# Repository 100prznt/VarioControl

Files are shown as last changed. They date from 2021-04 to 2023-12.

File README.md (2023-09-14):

Temp2IoT wiring

# VarioControl
IoT pump control for Vario pumps with 0 - 10 V interface.

------------

## Current build state

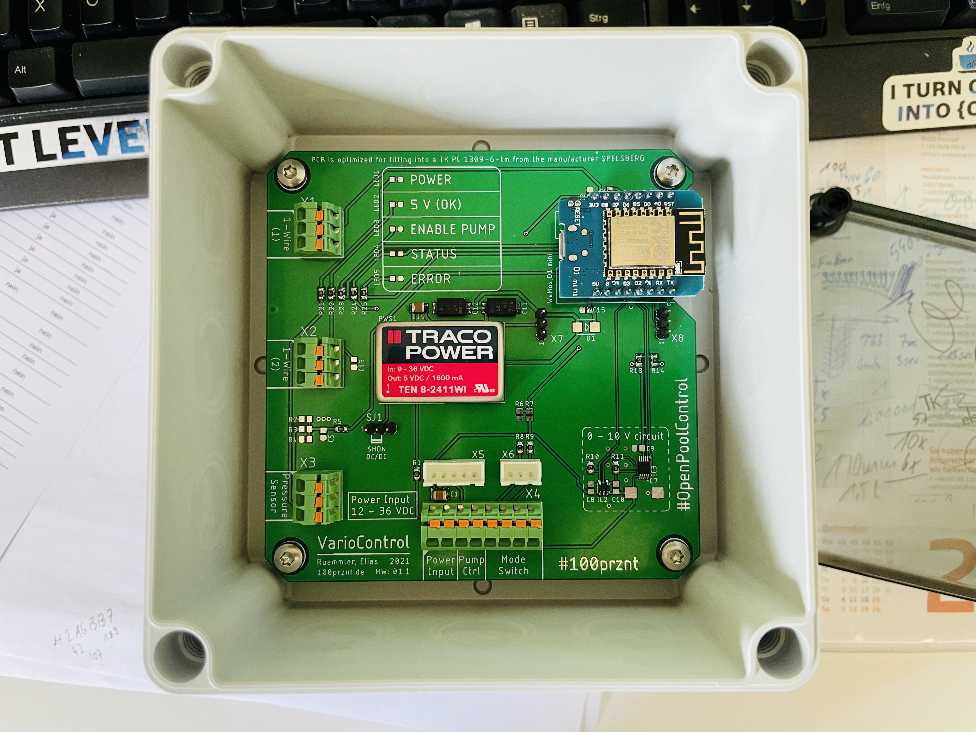
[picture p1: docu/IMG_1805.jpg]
VarioControl PCB v1.1 in Spelsberg enclosure

Unassembled PCB in matching Spelsberg enclosure. (2021/06/06)

## Hardware Features

+ 0 - 10 V interface for speed control of a Vario pump
+ WiFi interface
+ 1-wire interface for two DS18B20 temperature sensors
+ 0 - 10 V input for a pressure sensor (alt. also 0 - 5 V or 4 - 20 mA possible)
+ Switch input for operating mode preselection (AUTO - OFF - MANUAL)
+ 5 LEDs for status visualization
+ Wide range power supply (12 - 36 V)

## PCB

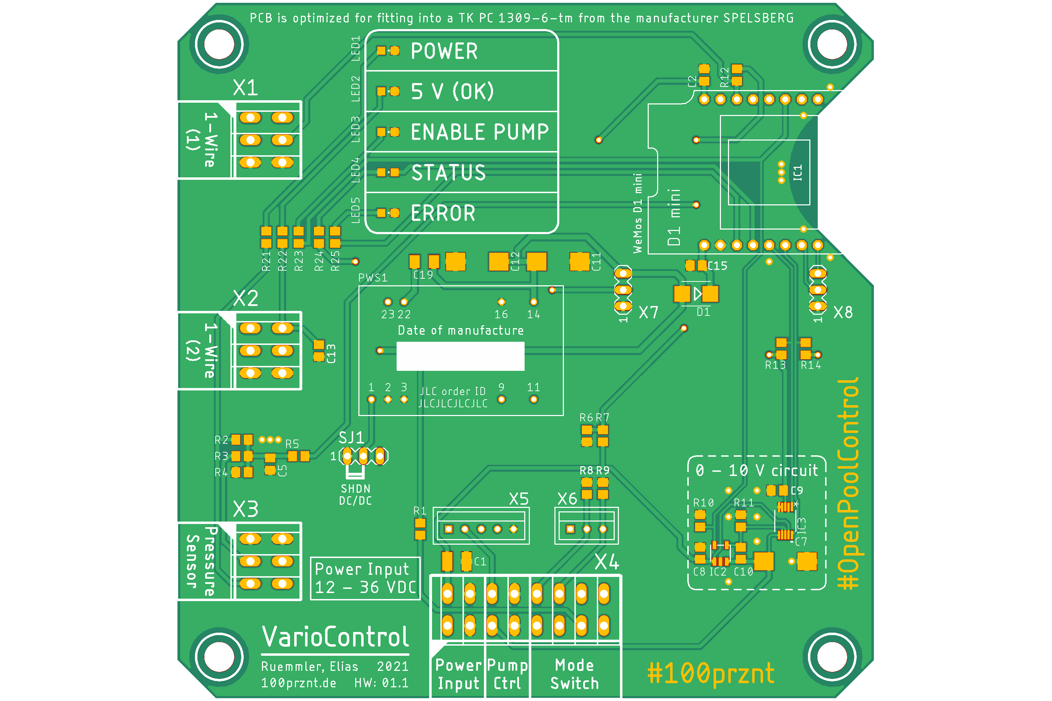
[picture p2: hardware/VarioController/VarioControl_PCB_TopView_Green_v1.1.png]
VarioControl PCB TopView v1.1


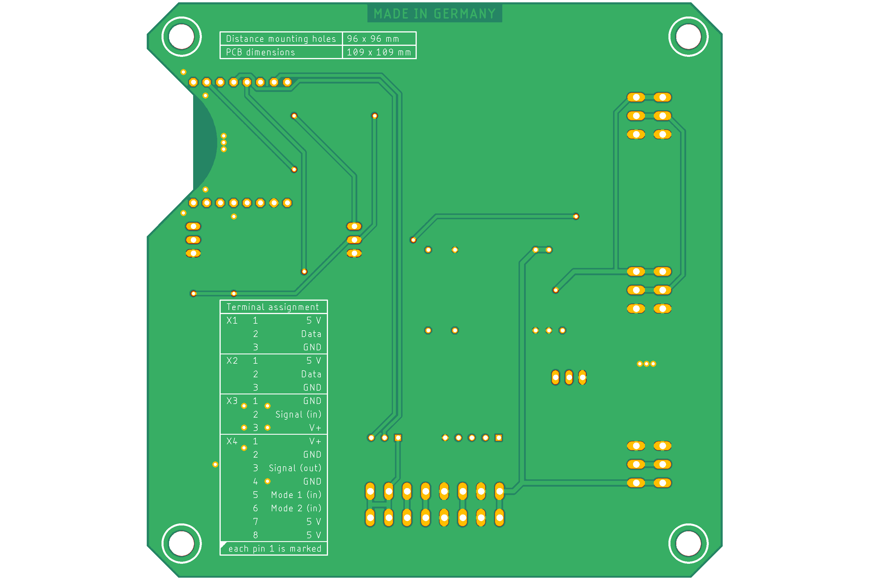
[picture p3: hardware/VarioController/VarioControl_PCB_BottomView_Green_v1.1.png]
VarioControl PCB BottomView v1.1


## AquaTechnix AquaVarioPlus

### Setup

The external control of the AquaVarioPlus can be activated in the setup menu of the pump. This is described in detail in the manual (of the BADU Eco Soft, which has the same control) on page 9 an 10. The "Steuerart" (control type) 0 - 10 V, code 3 is required.

* [Manual BADU EcoSoft](docu/BA_BADU_EcoSoft.pdf)

### Connector

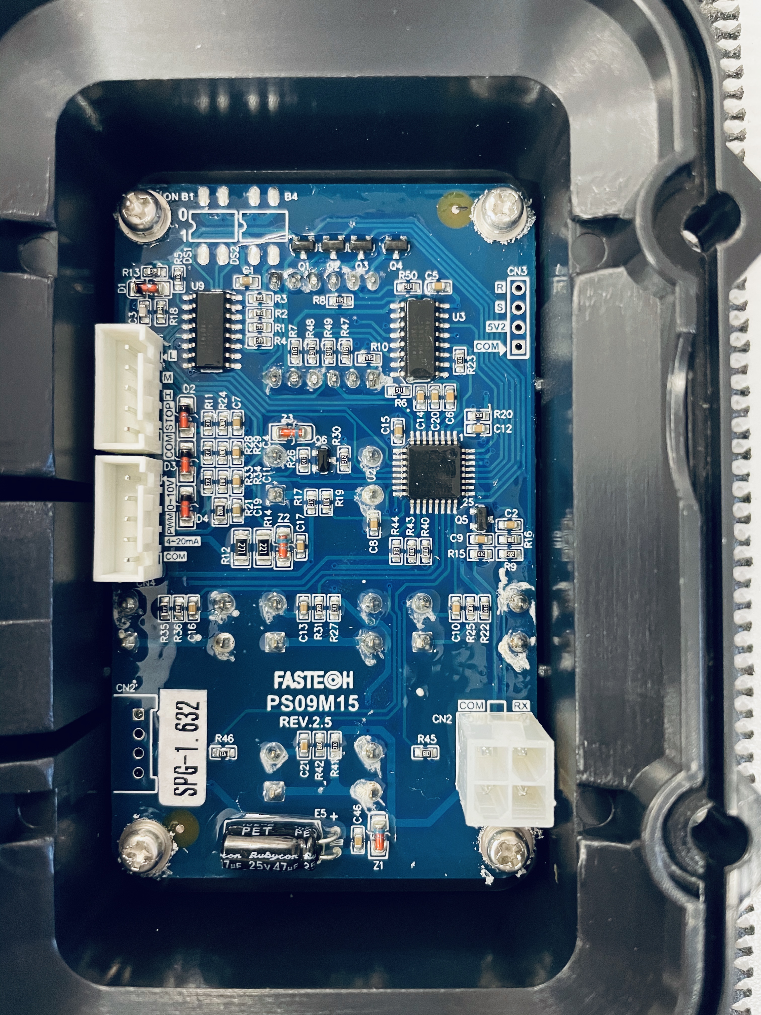
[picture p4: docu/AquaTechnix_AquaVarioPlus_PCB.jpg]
AquaVarioPlus PCB

Control board of the AquaVarioPlus pump from AquaTechnix.

The CN4 (pin 2) connector is provided for controlling the pump via the 0 - 10 V interface. See also [Manual BADU EcoSoft](docu/BA_BADU_EcoSoft.pdf) on page 7.

#### Pinning

| pin# | function | specification | in use with VarioControl | 
|-----:|:---|:---|:---:|
| 1 | n/a | | :heavy_multiplication_x: |
| 2 | rpm value (U) | 0 - 10 V | :heavy_check_mark: |
| 3 | PWM | unknow specs? | :heavy_multiplication_x: |
| 4 | rpm value (I) | 4 - 20 mA | :heavy_multiplication_x: |
| 5 | GND | | :heavy_check_mark: |

The control via the "PWM" input I have experimented with a frequency generator with various settings, unfortunately without success. I believe that the software implementation and a corresponding preselection of the control type is missing here.

#### Type
The plug used is probably a clone of the JST XH connector series, which has been modified to add an external locking mechanism. Plugs of this type are tricky to find, but an original XH plug from JST fits and holds very well.

| Manufacturer | SKU |
|:---|:---|
| JST (JAPAN SOLDERLESS TERMINALS) | __XHP-5__ |

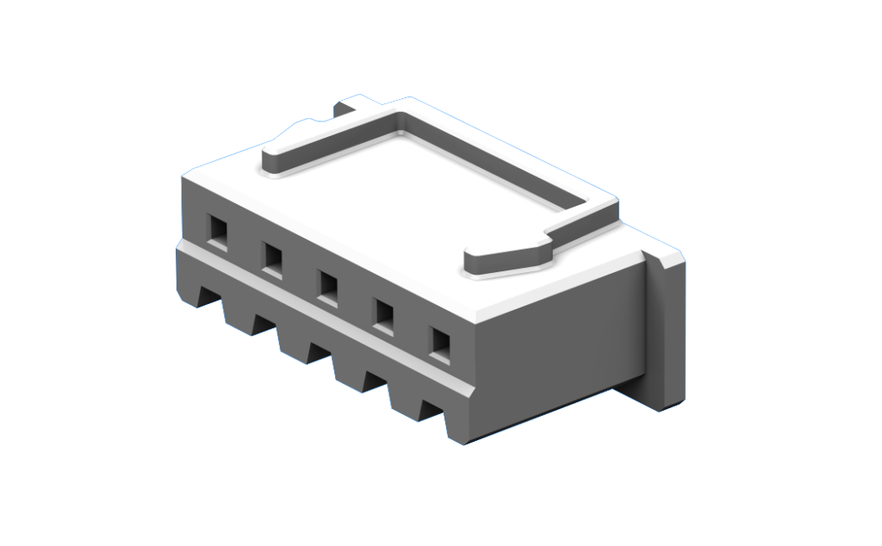
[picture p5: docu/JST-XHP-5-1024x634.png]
JST XHP-5.png


Suitable contacts are listed in the data sheet on page 2.

* [Datasheet JST XH Connector](docu/jst-xh.pdf)

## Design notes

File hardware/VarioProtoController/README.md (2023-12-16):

# ESPHome VarioProtoController

Um die Integration des __Vario Controllers__ in Home Assistant zu vereinfachen, soll die Hardware vollumfänglich mit __ESPHome__ kompatibel sein.

## Referenzen
* [Home Assistant](https://www.home-assistant.io/)
* [ESPHome](https://esphome.io/)

## BOM
Alle Komponenten des Prototyps kommen vom Hersteller DFRobot und können ohne Löten* miteinender verbunden werden.
* DAC 0-10 V [DFR0971](https://www.dfrobot.com/product-2613.html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)
* ADC [DFR0553](https://www.dfrobot.com/product-1730.html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)
* IO Shild [DFR0762](https://www.dfrobot.com/product-2395.html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)
* ESP32 [DFR0654](https://www.dfrobot.com/product-2231.html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)
* DS18B20 [KIT0021](https://www.dfrobot.com/product-1354.html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)

\*) Für den Anschluss der Temperatursensoren (DS18B20) ohne das DFRobot Gravity Shild müssen die Sensoren direkt mit einem entsprechenden Stecker (3-pin 2,54 mm) versehen werden.

## Aufbau
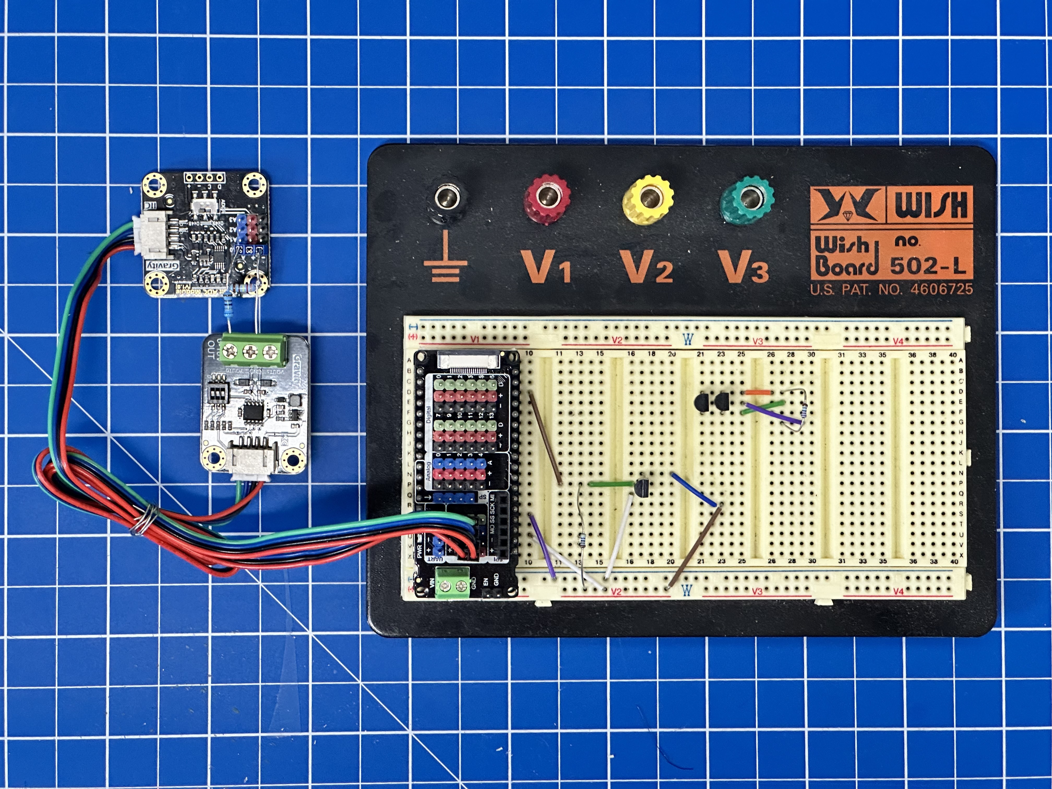
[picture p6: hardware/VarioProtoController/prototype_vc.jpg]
Aufbau der Komponenten


## Funktionen
### Übersicht
* Steuerung der Pumpe über 0 - 10 V Schnittstelle
* Eingang für 4 analoge Sensoren (z.B. Drucksensoren)
* Temperaturerfassung mit DS18B20 Sensoren

### DAC

### ADC
* Eingangsspannung ADS1115 min.: GND – 0.3
* Eingangsspannung ADS1115 max.: VDD + 0.3

Für den Anschluss von Sensoren mit 0 - 10 V Schnittstelle ist ein Spannungsteiler vorzusehen.

## ESPHome
https://community.home-assistant.io/t/esphome-configuration-for-pwm-to-0-10v-output-sensor-and-control/296445/8

### Sensoren
* Drehzahl
* Druck (1)
* Temperatur (1)

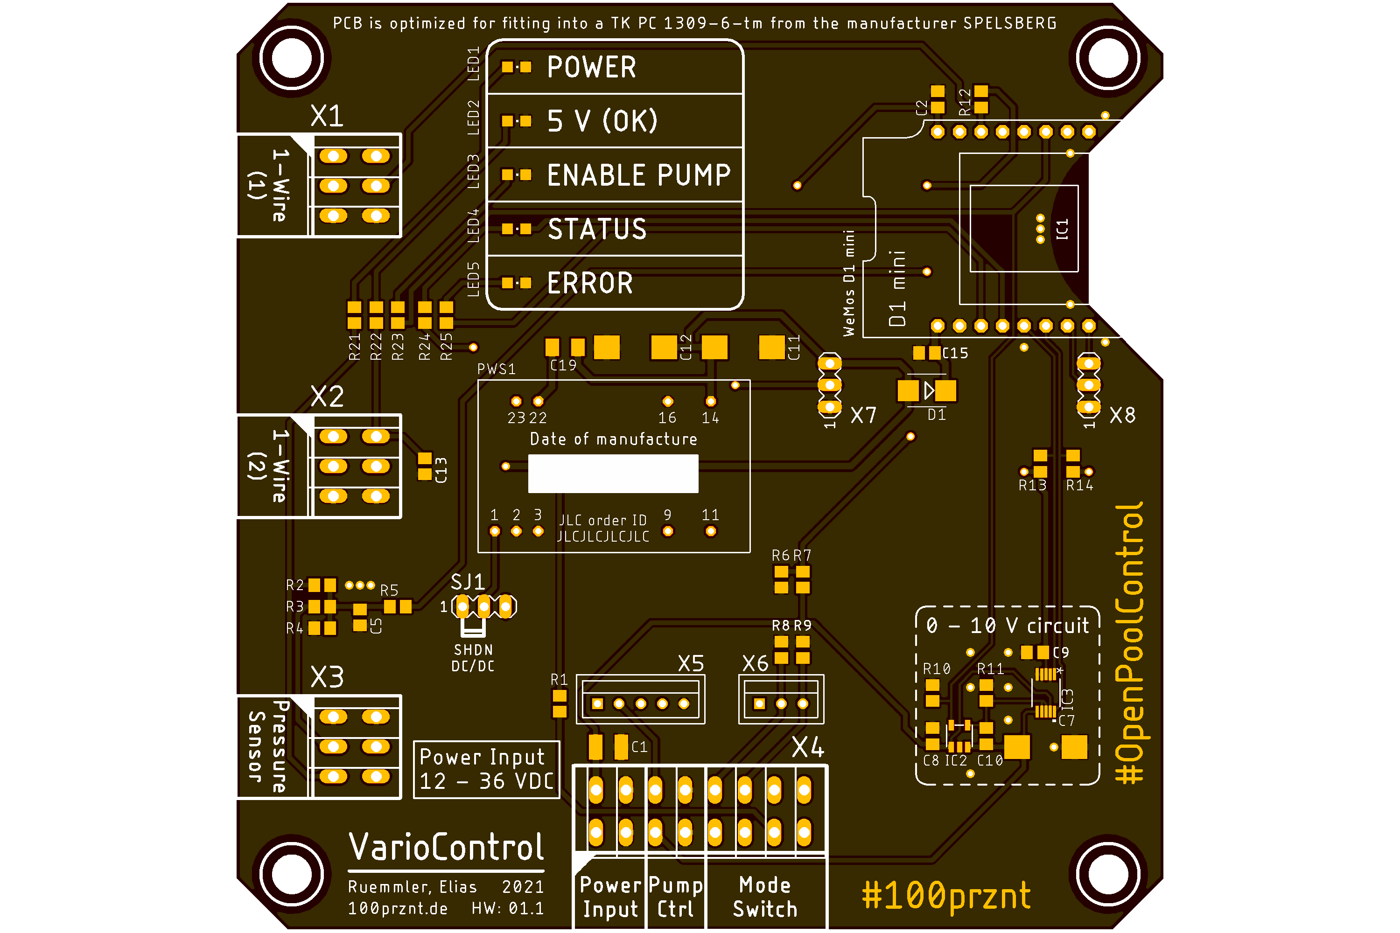
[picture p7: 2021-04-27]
hardware/VarioController/VarioControl_PCB_TopView_Black_v1.1.png

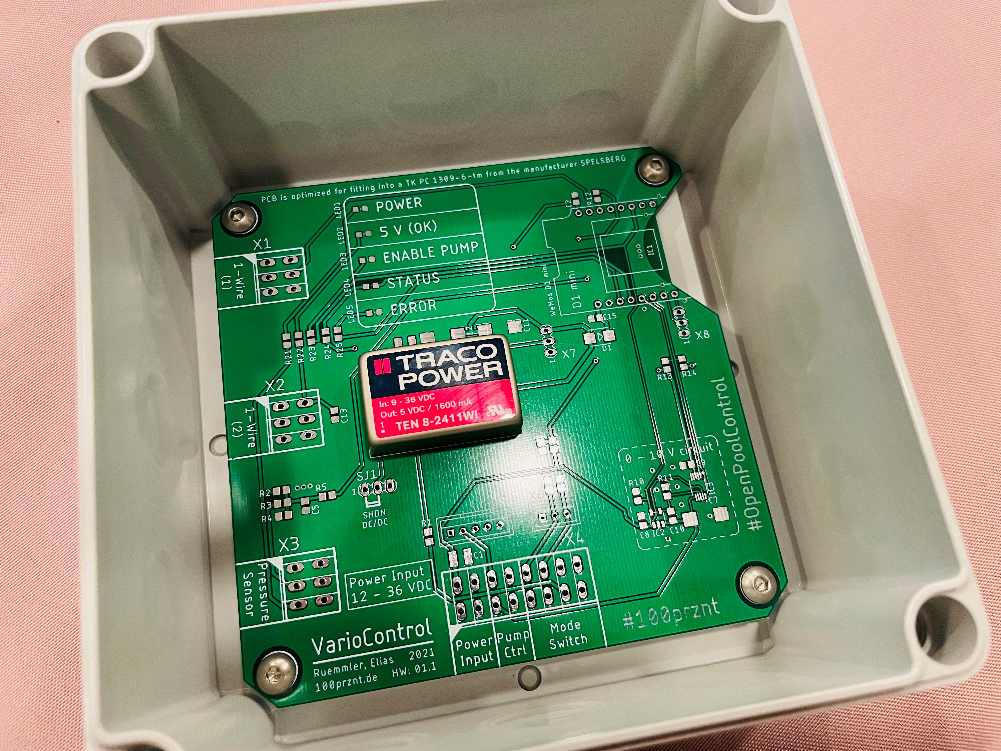
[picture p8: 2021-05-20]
docu/PCB_Unbestueckt_HW01_1_landscape.jpg

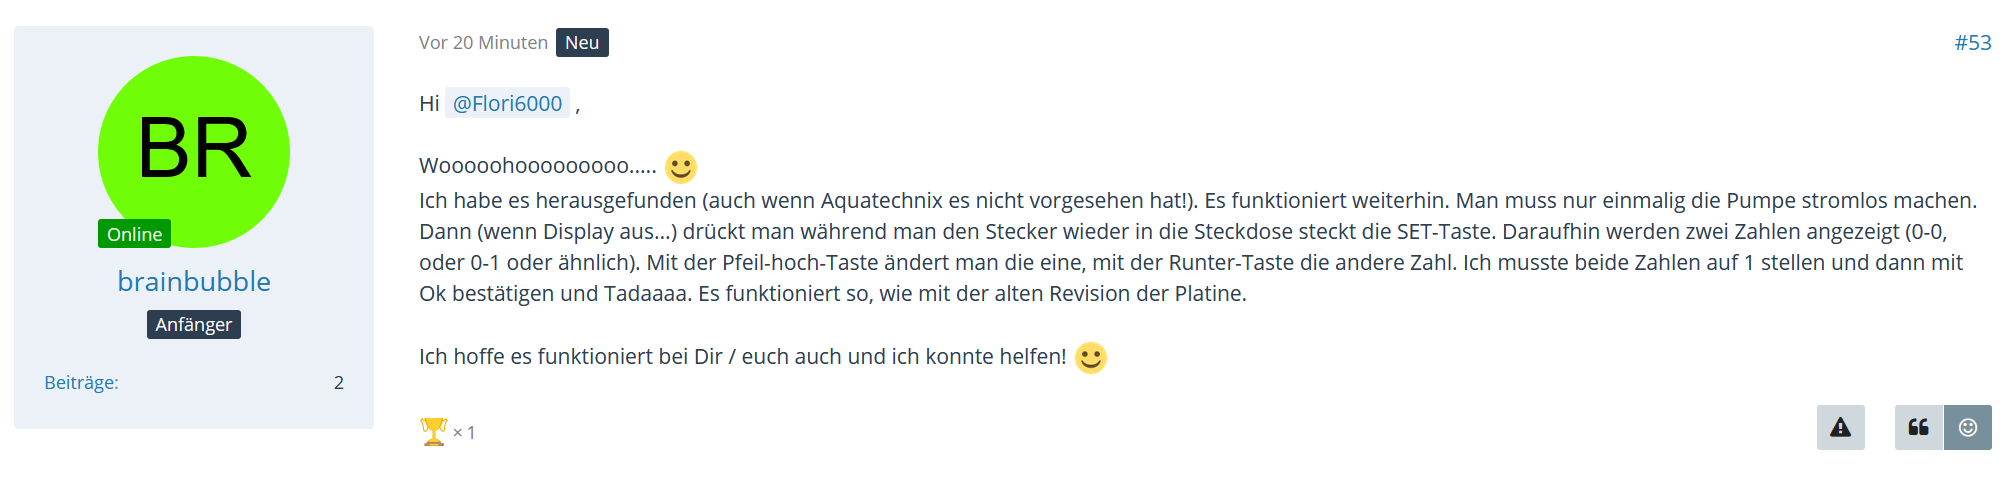
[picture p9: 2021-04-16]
docu/PPS_F_Hinweis_Umstellung_AquaVarioPlus.png

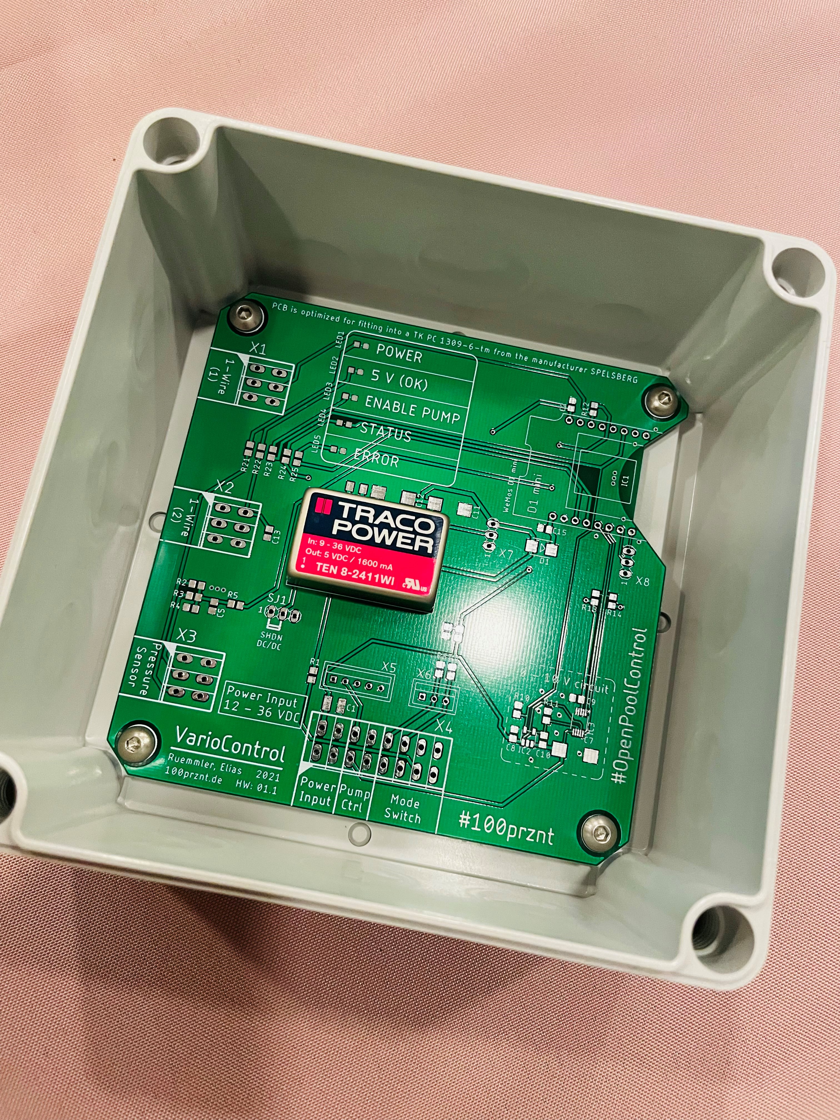
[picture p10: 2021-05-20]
docu/PCB_Unbestueckt_HW01_1_portrait.jpg

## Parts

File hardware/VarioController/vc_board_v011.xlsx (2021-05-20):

Part | Value | Device | Package | Description | BUILT_BY | DNAME | FARNELL_SKU | HOUSEPART | MANUFACTURER_PART_NUMBER | MF | MPN | OC_FARNELL | OC_NEWARK | POPULARITY | POPULATE | REVISION | REVNUM | SOURCELIBRARY | SPICEPREFIX | URL | VALUE | VENDOR
C1 | 1u/50V | C-EUC1210K | C1210K | CAPACITOR, European symbol |  |  |  |  |  |  |  |  |  | 0 |  |  |  |  | C
C2 | 100n/25V | C-EUC0805 | C0805 | CAPACITOR, European symbol |  |  |  |  |  |  |  |  |  | 88 |  |  |  |  | C
C5 | 100n/25V | C-EUC0805 | C0805 | CAPACITOR, European symbol |  |  |  |  |  |  |  |  |  | 88 |  |  |  |  | C
C7 | 4u7/50V | CPOL-EUD/7343-31W | D/7343-31W | POLARIZED CAPACITOR, European symbol |  |  |  |  |  |  |  |  |  | 1 |  |  |  |  | C
C8 | 100n/25V | C-EUC0805 | C0805 | CAPACITOR, European symbol |  |  |  |  |  |  |  |  |  | 88 |  |  |  |  | C
C9 | 100n/25V | C-EUC0805 | C0805 | CAPACITOR, European symbol |  |  |  |  |  |  |  |  |  | 88 |  |  |  |  | C
C10 | 100n/25V | C-EUC0805 | C0805 | CAPACITOR, European symbol |  |  |  |  |  |  |  |  |  | 88 |  |  |  |  | C
C11 |  | CPOL-EUD/7343-31W | D/7343-31W | POLARIZED CAPACITOR, European symbol |  |  |  |  |  |  |  |  |  | 1 |  |  |  |  | C
C12 |  | CPOL-EUD/7343-31W | D/7343-31W | POLARIZED CAPACITOR, European symbol |  |  |  |  |  |  |  |  |  | 1 |  |  |  |  | C
C13 | 100n/25V | C-EUC0805 | C0805 | CAPACITOR, European symbol |  |  |  |  |  |  |  |  |  | 88 |  |  |  |  | C
C15 | 100n/25V | C-EUC0805 | C0805 | CAPACITOR, European symbol |  |  |  |  |  |  |  |  |  | 88 |  |  |  |  | C
C19 | 1000p/2KV | C-EUC1206K | C1206K | CAPACITOR, European symbol |  |  |  |  |  |  |  |  |  | 13 |  |  |  |  | C
D1 |  | DIODE-SMB | SMB | DIODE |  |  |  |  |  |  |  |  |  | 11
FRAME1 | MF_FRAMEDEFAULT | MF_FRAMEDEFAULT | MF_FRAME_DEFAULT | Library: MF_Aesthetics |  | Elias RÃ¼mmler |  | 0 |  |  |  |  |  |  | 0 |  | REV: 1.01
IC1 | WeMos D1 mini | D1_MINI | D1_MINI |  |  |  |  |  |  |  |  |  |  |  |  |  |  |  |  |  | WeMos D1 mini
IC2 | MP2016DJ | MP2016 | TSOT23-5 | MP2016The MP2016 is a low power linear regulator that supplies power to systems with high voltage batteries. It includes a wide 4V to 42V input range, low dropout voltage and low quiescent supply current. |  |  |  |  |  |  |  |  |  |  |  |  |  |  |  |  | MP2016DJ
IC3 | DS3502U+ | DS3502U+ | 21-0061L_MXM |  | EMA_UL_Team |  |  |  | ds3502u+ |  |  |  |  |  |  | 2 |  | Maxim_2009-12-17_1 |  |  |  | Maxim Integrated Products
LED1 | GN 2,65V/2mA | LEDCHIPLED_0805 | CHIPLED_0805 | LED |  |  | 2846598 |  |  |  |  |  |  | 52
LED2 | GN 2,65V/2mA | LEDCHIPLED_0805 | CHIPLED_0805 | LED |  |  | 2846598 |  |  |  |  |  |  | 52
LED3 | GE 1,85V/2mA | LEDCHIPLED_0805 | CHIPLED_0805 | LED |  |  | 2846596 |  |  |  |  |  |  | 52
LED4 | BL 2,65V/2mA | LEDCHIPLED_0805 | CHIPLED_0805 | LED |  |  | 2846594 |  |  |  |  |  |  | 52
LED5 | RT 1.95V/2mA | LEDCHIPLED_0805 | CHIPLED_0805 | LED |  |  | 2099241 |  |  |  |  |  |  | 52
PWS1 | TEN 8-2411WI | TEN8WI | TEN8
R1 | 120R | R-EU_R0805 | R0805 | RESISTOR, European symbol |  |  |  |  |  |  |  |  |  | 86 |  |  |  |  | R
R2 | N/A | R-EU_R0805 | R0805 | RESISTOR, European symbol |  |  |  |  |  |  |  |  |  | 86 |  |  |  |  | R
R3 | 6K8 0,1% | R-EU_R0805 | R0805 | RESISTOR, European symbol |  |  |  |  |  |  |  |  |  | 86 |  |  |  |  | R
R4 | 3K1 0,1% | R-EU_R0805 | R0805 | RESISTOR, European symbol |  |  |  |  |  |  |  |  |  | 86 |  |  |  |  | R
R5 | 120R | R-EU_R0805 | R0805 | RESISTOR, European symbol |  |  |  |  |  |  |  |  |  | 86 |  |  |  |  | R
R6 |  | R-EU_R0805 | R0805 | RESISTOR, European symbol |  |  |  |  |  |  |  |  |  | 86 |  |  |  |  | R
R7 |  | R-EU_R0805 | R0805 | RESISTOR, European symbol |  |  |  |  |  |  |  |  |  | 86 |  |  |  |  | R
R8 | 10K | R-EU_R0805 | R0805 | RESISTOR, European symbol |  |  |  |  |  |  |  |  |  | 86 |  |  |  |  | R
R9 | 10K | R-EU_R0805 | R0805 | RESISTOR, European symbol |  |  |  |  |  |  |  |  |  | 86 |  |  |  |  | R
R10 | 10K | R-EU_R0805 | R0805 | RESISTOR, European symbol |  |  |  |  |  |  |  |  |  | 86 |  |  |  |  | R
R11 | 1K3 | R-EU_R0805 | R0805 | RESISTOR, European symbol |  |  |  |  |  |  |  |  |  | 86 |  |  |  |  | R
R12 | 10K | R-EU_R0805 | R0805 | RESISTOR, European symbol |  |  |  |  |  |  |  |  |  | 86 |  |  |  |  | R
R13 | 10K | R-EU_R0805 | R0805 | RESISTOR, European symbol |  |  |  |  |  |  |  |  |  | 86 |  |  |  |  | R
R14 | 10K | R-EU_R0805 | R0805 | RESISTOR, European symbol |  |  |  |  |  |  |  |  |  | 86 |  |  |  |  | R
R21 | 10K | R-EU_R0805 | R0805 | RESISTOR, European symbol |  |  |  |  |  |  |  |  |  | 86 |  |  |  |  | R
R22 | 1K2 | R-EU_R0805 | R0805 | RESISTOR, European symbol |  |  |  |  |  |  |  |  |  | 86 |  |  |  |  | R
R23 | 680R | R-EU_R0805 | R0805 | RESISTOR, European symbol |  |  |  |  |  |  |  |  |  | 86 |  |  |  |  | R
R24 | 330R | R-EU_R0805 | R0805 | RESISTOR, European symbol |  |  |  |  |  |  |  |  |  | 86 |  |  |  |  | R
R25 | 680R | R-EU_R0805 | R0805 | RESISTOR, European symbol |  |  |  |  |  |  |  |  |  | 86 |  |  |  |  | R
SJ1 |  | MA03-1 | MA03-1 | PIN HEADER |  |  |  |  |  |  |  | unknown | unknown | 48
X1 | SPTAF_1/3_3,5 | SPTAF_1/3_3,5 | SPTAF_1/3_3,5 | Leiterplattenklemme - SPTAF 1/ 3-3,5-IL
X2 | SPTAF_1/3_3,5 | SPTAF_1/3_3,5 | SPTAF_1/3_3,5 | Leiterplattenklemme - SPTAF 1/ 3-3,5-IL
X3 | SPTAF_1/3_3,5 | SPTAF_1/3_3,5 | SPTAF_1/3_3,5 | Leiterplattenklemme - SPTAF 1/ 3-3,5-IL
X4 | SPTAF_1/8_3,5 | SPTAF_1/8_3,5 | SPTAF_1/8_3,5 | Leiterplattenklemme - SPTAF 1/ 8-3,5-IL - 1861991 |  |  |  |  |  | FARNELL | 1861991 | 2580663 | 71C4133
X5 | 05-JST-B5B-XH-A | 05-JST-B5B-XH-A | B5B-XH | JST CONNECTOR
X6 | 03-JST-B3B-XH-A | 03-JST-B3B-XH-A | B3B-XH | JST CONNECTOR
X7 |  | MA03-1 | MA03-1 | PIN HEADER |  |  |  |  |  |  |  | unknown | unknown | 48
X8 |  | MA03-1 | MA03-1 | PIN HEADER |  |  |  |  |  |  |  | unknown | unknown | 48

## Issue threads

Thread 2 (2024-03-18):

Frage zu Pumpensteuerung

AzonInc, 2024-03-18:
Hi,

kann man damit ggfs. auch die eingestellte Pumpengeschwindigkeit auslesen?

Und könnte man die Pumpe ggfs auch per PWM Signal steuern? Ich habe leider keine Dokumentation zu dem Board gefunden. Es ist eine Aqua Vario Plus Filterpumpe.

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

Grüße
Florian

100prznt, 2024-03-19:
Habe zahlreiche versuche unternommen und bin zu dem Schluss gekommen, dass der PWM Pin bei der Aqua Vario Plus ohne Funktion ist, bzw. sich nicht per Software aktivieren lässt.

Generell lässt sich nichts auslesen, es sind alles Eingänge. Wenn die Pumpe ferngesteuert wird, muss ja aber auch nichts zurück gelesen werden. Die Sollwerte stehen ja im Controller (VarioControl) bereit und können jederzeit rück gelesen werden.
Ein Mischbetrieb (mit manueller Steuerung über die Taster an der Pumpe) wird nicht unterstützt.

Beste Grüße Elias

AzonInc, 2024-03-21:
Schade, aber danke für die Info :)

Closed 2024-03-21.

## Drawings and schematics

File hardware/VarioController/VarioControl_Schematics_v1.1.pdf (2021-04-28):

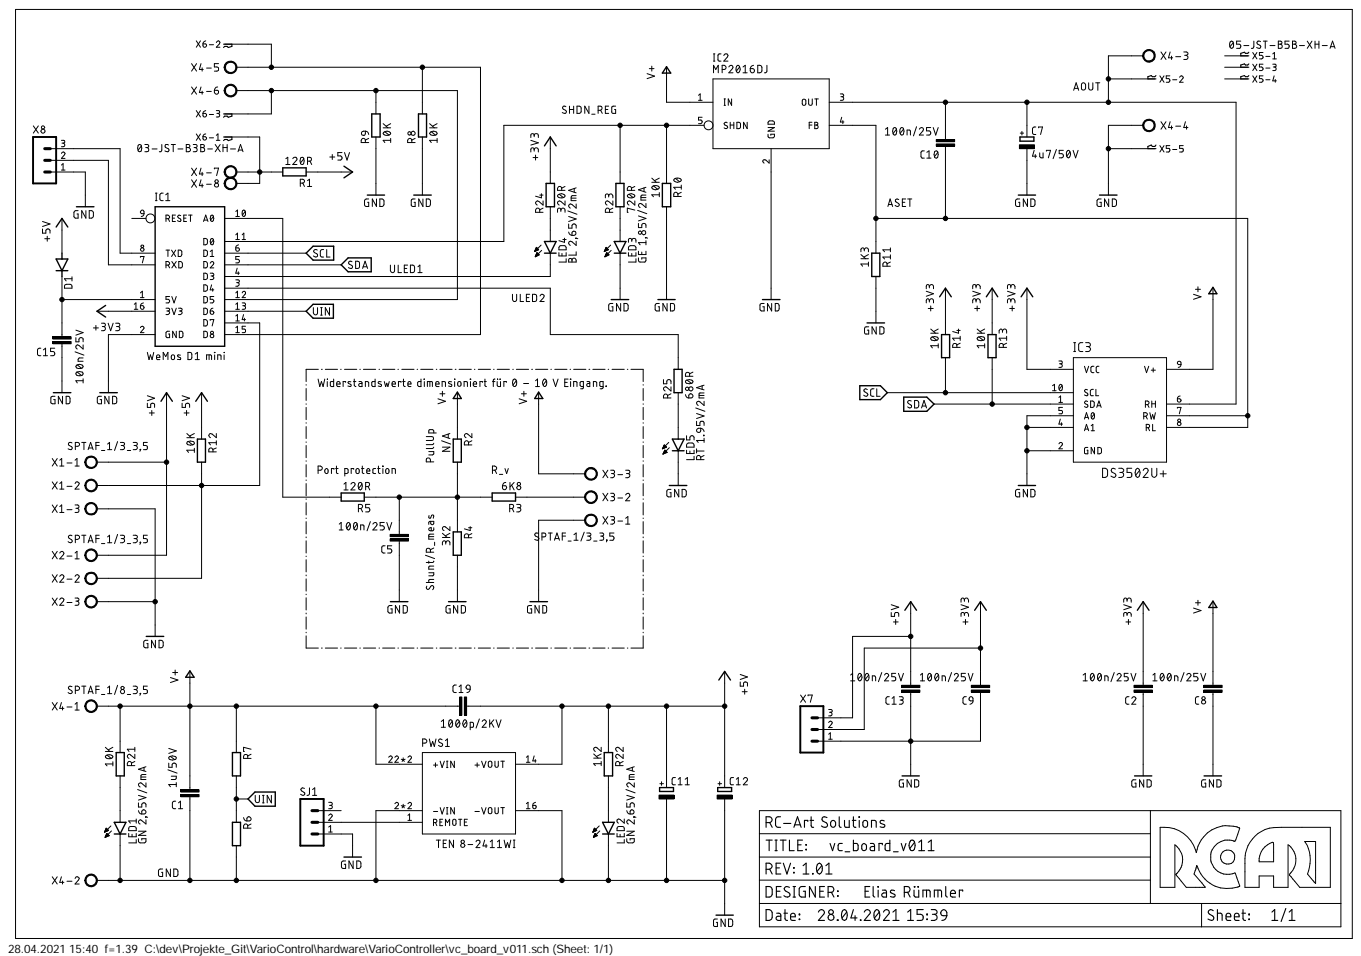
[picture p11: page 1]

28.04.2021 15:40 f=1.39 C:\dev\Projekte_Git\VarioControl\hardware\VarioController\vc_board_v011.sch (Sheet: 1/1)

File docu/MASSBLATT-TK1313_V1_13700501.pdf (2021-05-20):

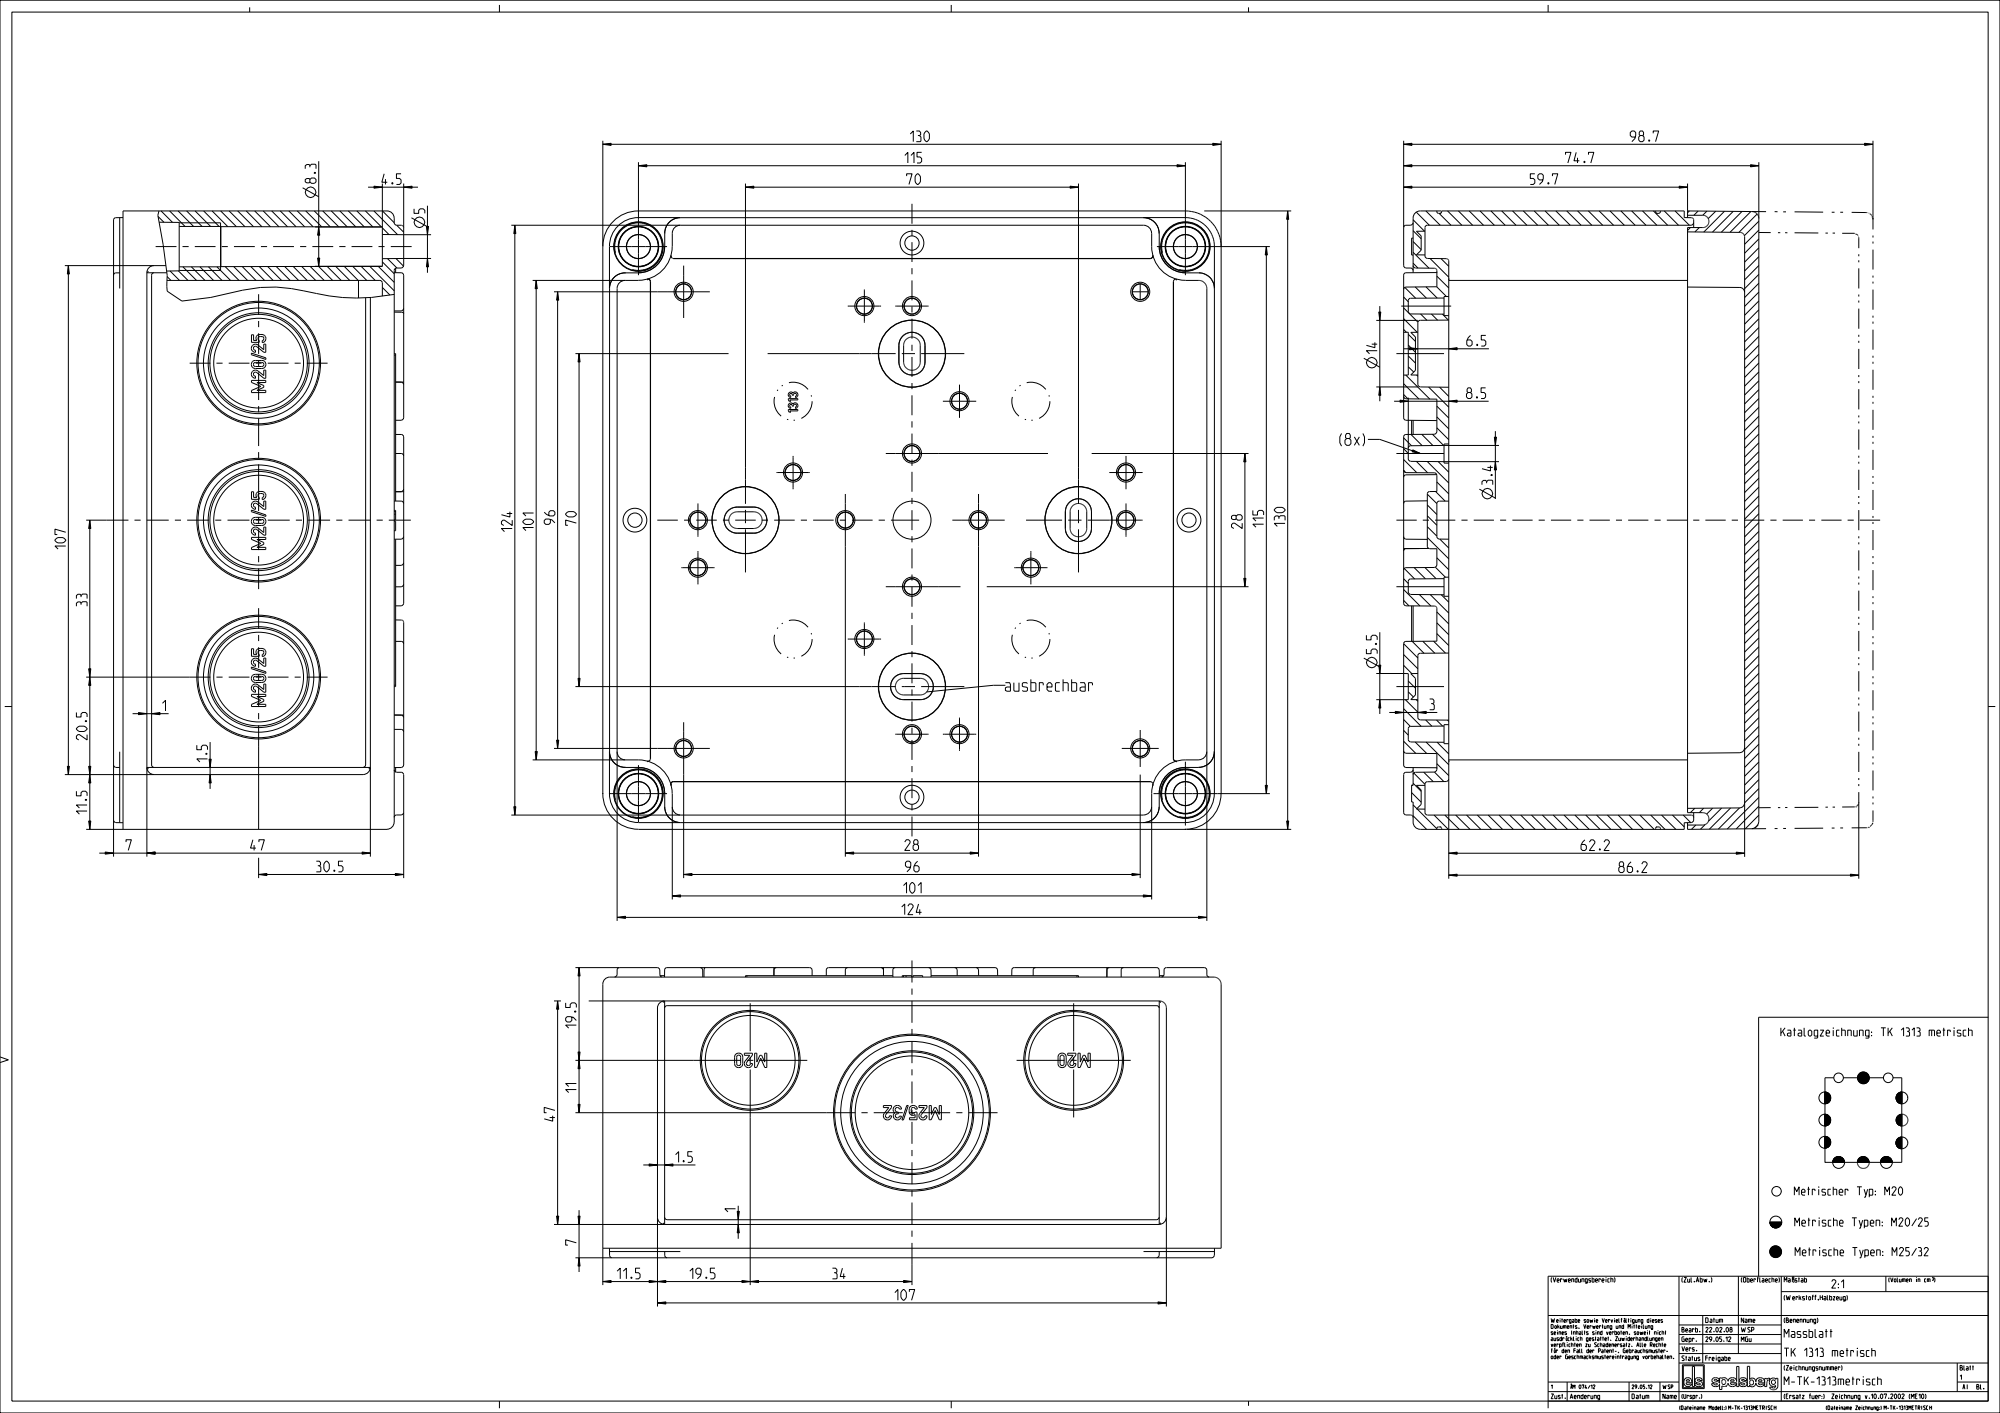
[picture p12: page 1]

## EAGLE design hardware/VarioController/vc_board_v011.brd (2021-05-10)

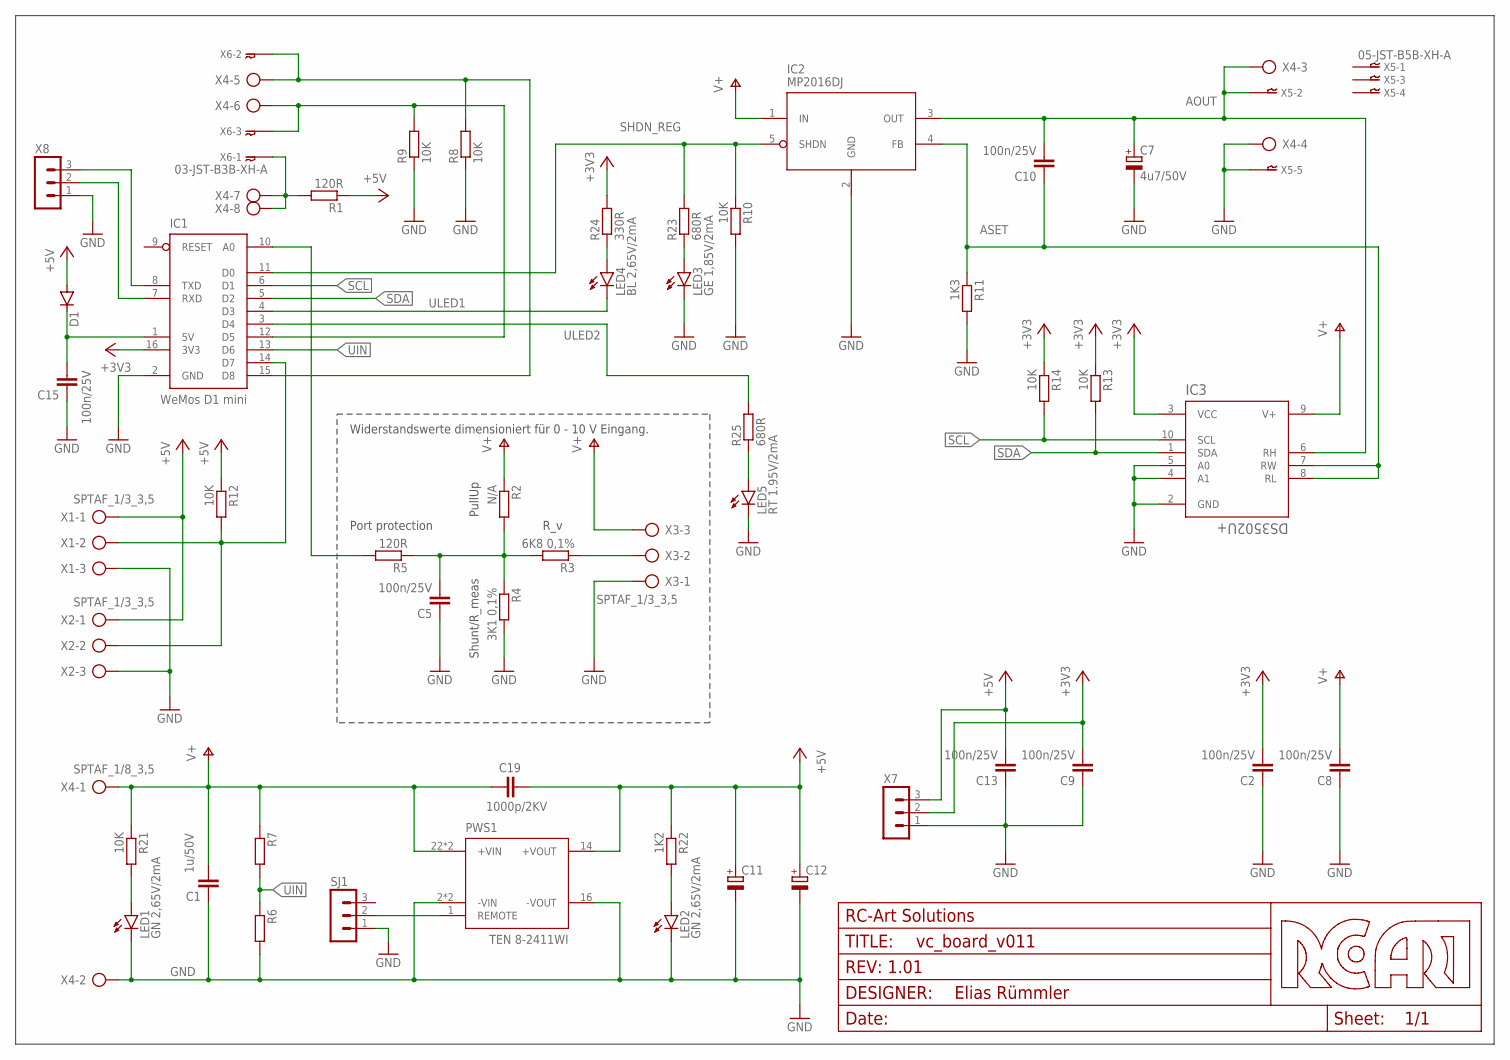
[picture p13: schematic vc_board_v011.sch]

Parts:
C1: 1u/50V; C1210K
C2, C5, C8, C9, C10, C13, C15: 100n/25V; C0805
C7: 4u7/50V; D/7343-31W
C11, C12: CPOL-EUD/7343-31W; D/7343-31W
C19: 1000p/2KV; C1206K
D1: DIODE-SMB; SMB
FRAME1: MF_FRAMEDEFAULT; MF_FRAME_DEFAULT
IC1: WeMos D1 mini; D1_MINI
IC2: MP2016DJ; TSOT23-5
IC3: DS3502U+; 21-0061L_MXM
LED1, LED2: GN 2,65V/2mA; CHIPLED_0805; FARNELL_SKU 2846598
LED3: GE 1,85V/2mA; CHIPLED_0805; FARNELL_SKU 2846596
LED4: BL 2,65V/2mA; CHIPLED_0805; FARNELL_SKU 2846594
LED5: RT 1.95V/2mA; CHIPLED_0805; FARNELL_SKU 2099241
PWS1: TEN 8-2411WI; TEN8
R1, R5: 120R; R0805
R2: N/A; R0805
R3: 6K8 0,1%; R0805
R4: 3K1 0,1%; R0805
R6, R7: R-EU_R0805; R0805
R8, R9, R10, R12, R13, R14, R21: 10K; R0805
R11: 1K3; R0805
R22: 1K2; R0805
R23, R25: 680R; R0805
R24: 330R; R0805
SJ1: MA03-1
X1, X2, X3: SPTAF_1/3_3,5
X4: SPTAF_1/8_3,5
X5: 05-JST-B5B-XH-A; B5B-XH
X6: 03-JST-B3B-XH-A; B3B-XH
X7, X8: MA03-1

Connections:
+3V3: C2.2, C9.2, IC1.16 (3V3), IC3.3 (VCC), R13.1, R14.1, R24.2, X7.2
+5V: C11.+, C12.+, C13.2, C19.2, D1.A, PWS1.14 (+VOUT), R1.1, R12.1, R22.1, X1.1, X1.1A, X2.1, X2.1A, X7.3
AOUT: C7.+, C10.2, IC2.3 (OUT), IC3.6 (RH), X4.3, X4.3A, X5.P$2
ASET: C10.1, IC2.4 (FB), IC3.7 (RW), IC3.8 (RL), R11.1
GND: C1.1, C2.1, C5.1, C7.-, C8.1, C9.1, C11.-, C12.-, C13.1, C15.1, IC1.2 (GND), IC2.2 (GND), IC3.2 (GND), IC3.4 (A1), IC3.5 (A0), LED1.C, LED2.C, LED3.C, LED5.C, PWS1.2 (-VIN), PWS1.3 (-VIN), PWS1.16 (-VOUT), R4.2, R6.2, R8.1, R9.1, R10.2, R11.2, SJ1.1, X1.3, X1.3A, X2.3, X2.3A, X3.1, X3.1A, X4.2, X4.2A, X4.4, X4.4A, X5.P$5, X7.1, X8.1
unnamed: C5.2, R2.2, R3.2, R4.1, R5.1
unnamed: IC1.12 (D5), R9.2, X4.6, X4.6A, X6.P$3
unnamed: IC1.15 (D8), R8.2, X4.5, X4.5A, X6.P$2
unnamed: R1.2, X4.7, X4.7A, X4.8, X4.8A, X6.P$1
unnamed: R3.1, X3.2, X3.2A
unnamed: C15.2, D1.C, IC1.1 (5V)
unnamed: PWS1.1 (REMOTE), SJ1.2
unnamed: LED3.A, R23.1
unnamed: LED1.A, R21.2
unnamed: LED2.A, R22.2
unnamed: IC1.14 (D7), R12.2, X1.2, X1.2A, X2.2, X2.2A
unnamed: IC1.8 (TXD), X8.3
unnamed: IC1.7 (RXD), X8.2
unnamed: LED4.A, R24.1
unnamed: LED5.A, R25.1
unnamed: IC1.10 (A0), R5.2
SCL: IC1.6 (D1), IC3.10 (SCL), R14.2
SDA: IC1.5 (D2), IC3.1 (SDA), R13.2
SHDN_REG: IC1.11 (D0), IC2.5 (SHDN), R10.1, R23.2
UIN: IC1.13 (D6), R6.1, R7.2
ULED1: IC1.4 (D3), LED4.C
ULED2: IC1.3 (D4), R25.2
V+: C1.2, C8.2, C19.1, IC2.1 (IN), IC3.9 (V+), PWS1.22 (+VIN), PWS1.23 (+VIN), R2.1, R7.1, R21.1, X3.3, X3.3A, X4.1, X4.1A

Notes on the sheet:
PullUp
Shunt/R_meas
R_v
Port protection
Widerstandswerte dimensioniert für 0 - 10 V Eingang.

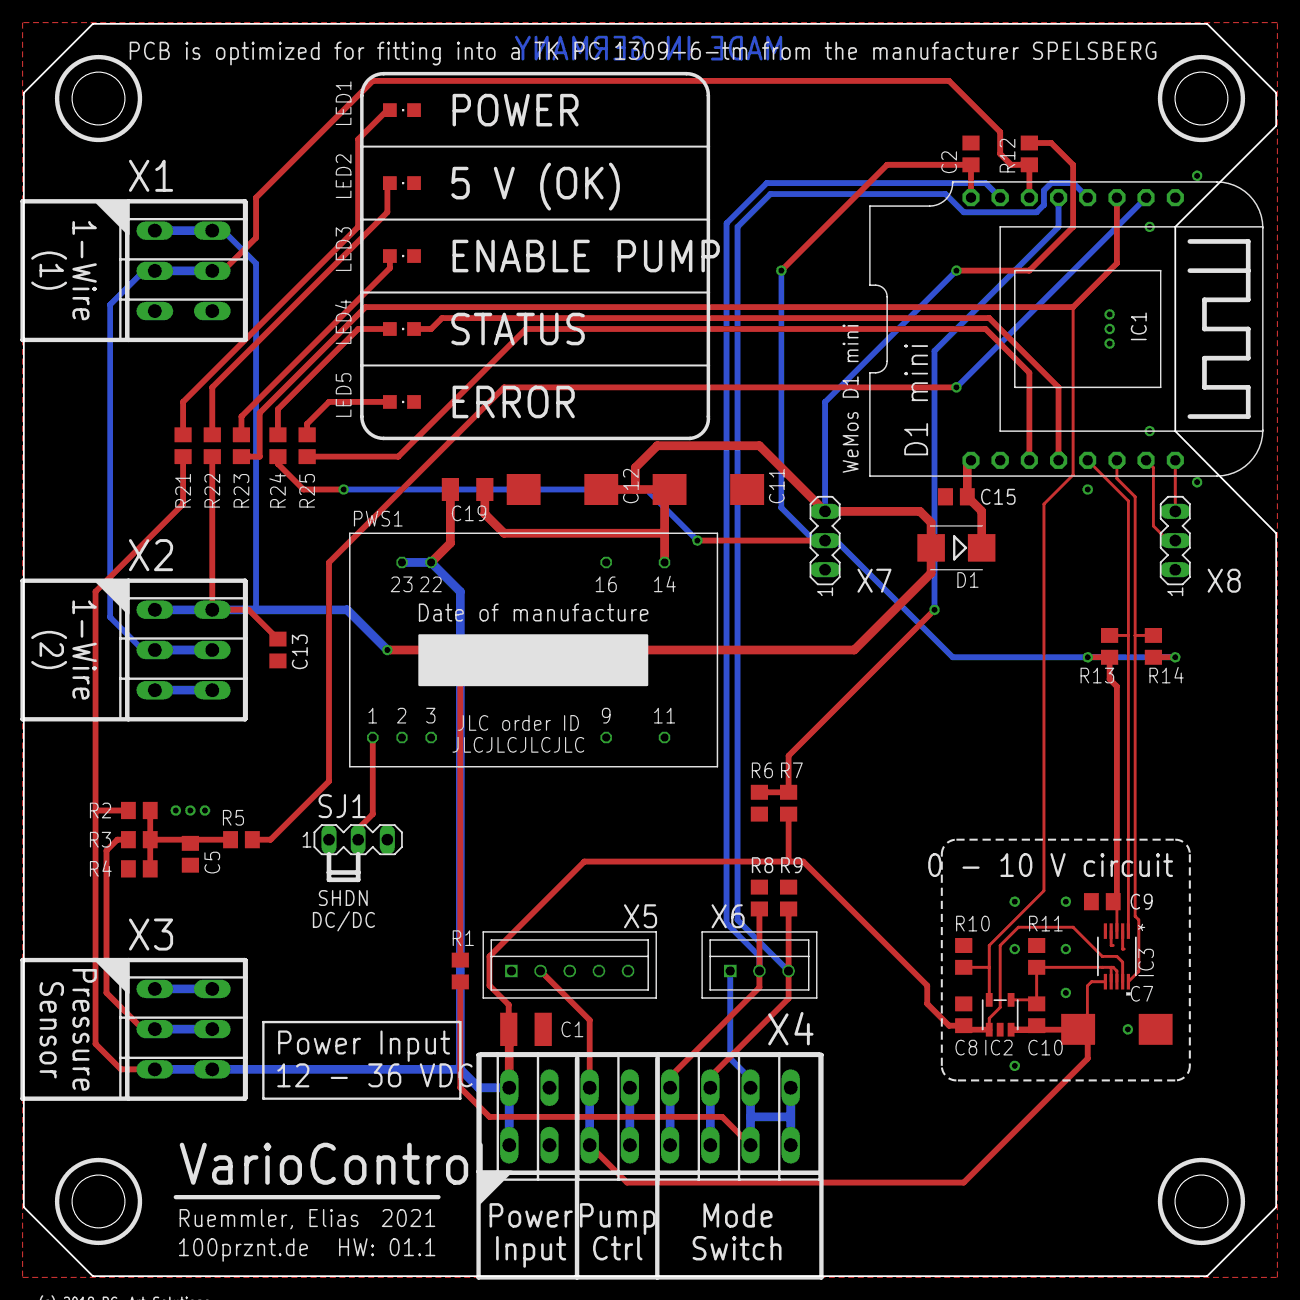
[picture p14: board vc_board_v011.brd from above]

Board: 2 copper layers, 109.0 x 109.0 mm, 51 parts (0 on the bottom side), 28 nets.

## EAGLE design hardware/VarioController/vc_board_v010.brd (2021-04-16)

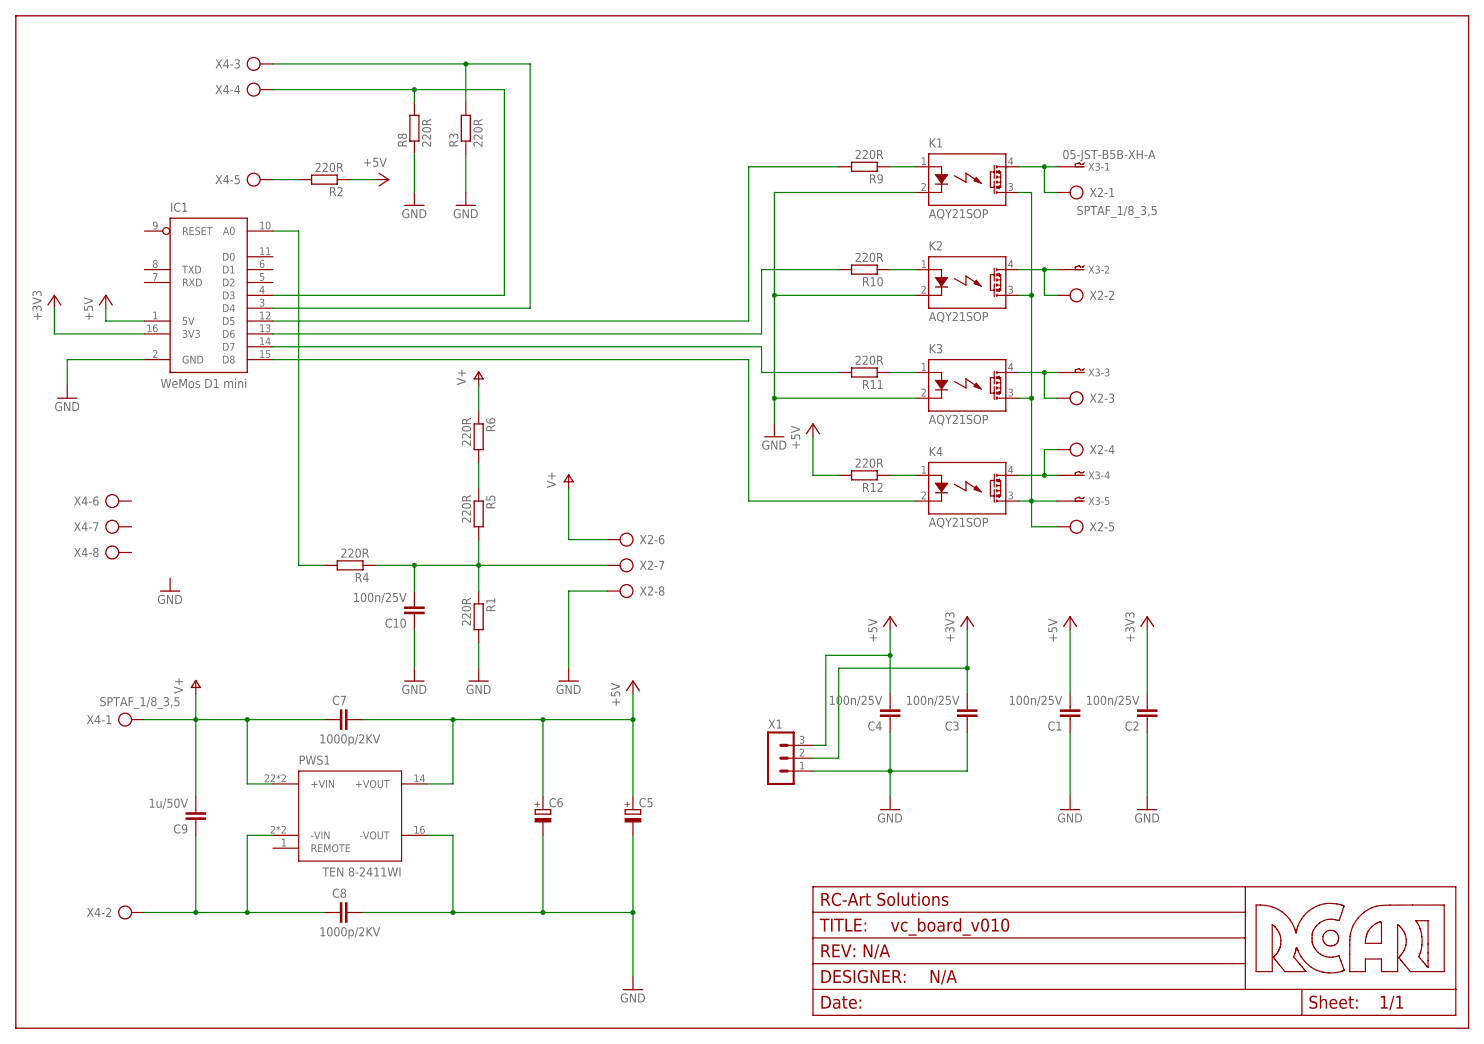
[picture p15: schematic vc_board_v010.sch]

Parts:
C1, C2, C3, C4, C10: 100n/25V; C0805
C5, C6: CPOL-EUCT7343; CT7343
C7, C8: 1000p/2KV; C1206K
C9: 1u/50V; C1210K
FRAME1: MF_FRAMEDEFAULT; MF_FRAME_DEFAULT
IC1: WeMos D1 mini; D1_MINI
K1, K2, K3, K4: AQY21SOP; SOP04
PWS1: TEN 8-2411WI; TEN8
R1, R2, R3, R4, R5, R6, R8, R9, R10, R11, R12: 220R; R0805
X1: MA03-1
X2, X4: SPTAF_1/8_3,5
X3: 05-JST-B5B-XH-A; B5B-XH

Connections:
+3V3: C2.2, C3.2, IC1.16 (3V3), X1.2
+5V: C1.2, C4.2, C5.+, C6.+, C7.2, IC1.1 (5V), PWS1.14 (+VOUT), R2.1, R12.2, X1.3
GND: C1.1, C2.1, C3.1, C4.1, C5.-, C6.-, C8.2, C10.1, IC1.2 (GND), K1.2 (K), K2.2 (K), K3.2 (K), PWS1.16 (-VOUT), R1.2, R3.1, R8.1, X1.1, X2.8, X2.8A
unnamed: C10.2, R1.1, R4.1, R5.2, X2.7, X2.7A
unnamed: IC1.4 (D3), R8.2, X4.4, X4.4A
unnamed: IC1.3 (D4), R3.2, X4.3, X4.3A
unnamed: C8.1, C9.1, PWS1.2 (-VIN), PWS1.3 (-VIN), X4.2, X4.2A
unnamed: R2.2, X4.5, X4.5A
unnamed: K1.3 (DS2), K2.3 (DS2), K3.3 (DS2), K4.3 (DS2), X2.5, X2.5A, X3.P$5
unnamed: K4.4 (DS1), X2.4, X2.4A, X3.P$4
unnamed: K3.4 (DS1), X2.3, X2.3A, X3.P$3
unnamed: K2.4 (DS1), X2.2, X2.2A, X3.P$2
unnamed: K1.4 (DS1), X2.1, X2.1A, X3.P$1
unnamed: K4.1 (A), R12.1
unnamed: R5.1, R6.2
unnamed: K3.1 (A), R11.1
unnamed: K2.1 (A), R10.1
unnamed: K1.1 (A), R9.1
unnamed: IC1.15 (D8), K4.2 (K)
unnamed: IC1.14 (D7), R11.2
unnamed: IC1.13 (D6), R10.2
unnamed: IC1.12 (D5), R9.2
unnamed: IC1.10 (A0), R4.2
V+: C7.1, C9.2, PWS1.22 (+VIN), PWS1.23 (+VIN), R6.1, X2.6, X2.6A, X4.1, X4.1A

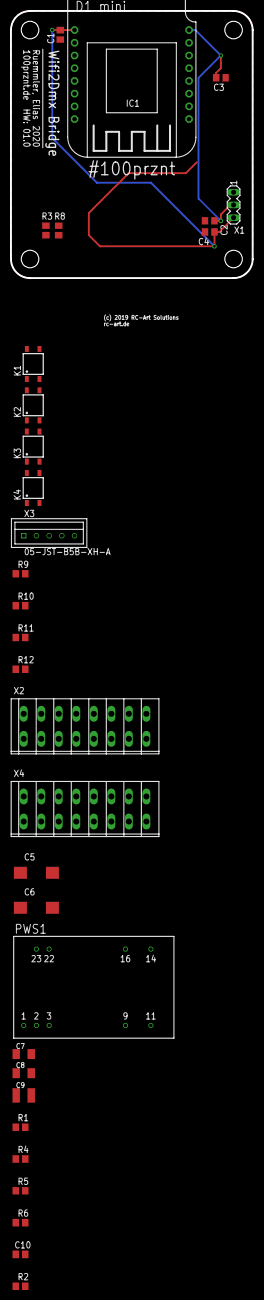
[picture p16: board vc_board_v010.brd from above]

Board: 2 copper layers, 48.3 x 53.3 mm, 32 parts (0 on the bottom side), 24 nets.

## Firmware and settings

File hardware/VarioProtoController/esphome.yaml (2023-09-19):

esphome:
  name: varioprotocontrol
  friendly_name: VarioProtoControl

esp32:
  board: esp32dev
  framework:
    type: arduino

# Enable logging
logger:

ota:
  password: !secret ota_password

wifi:
  ssid: !secret wifi_ssid
  password: !secret wifi_password

  # Enable fallback hotspot (captive portal) in case wifi connection fails
  ap:
    ssid: "VarioProtoControl"
    password: !secret ap_password

# Enable captive portal
captive_portal:

# Enable web server
#web_server:
#  port: 80
#  version: 2


# Enable Home Assistant API
api:
  encryption:
    key: !secret api_key
#  services:
#    - service: set_pumpe_sollwert_percent
#      variables:
#        percentage: int
#      then:
#        - lambda: |-
#            id(pump_percent) = percentage;
#            id(pump_percent_sensor).publish_state(percentage);

# Configuration for DFRobot FireBeetle 2 ESP32-E
i2c:
  sda: 21
  scl: 22
  scan: true
  id: bus_a

ads1115:
  - address: 0x48

gp8403:
  id: DFR0971
  voltage: 10V


number:
  - platform: template
    id: pump_power_number
    name: "Pumpenleistung"
    optimistic: true
    min_value: 0
    max_value: 100
    step: 1
    on_value:
      then:
        - lambda: |-
            id(pump_percent) = x;
            id(pump_percent_sensor).publish_state(x);

globals:
   - id: pump_percent
     type: float
     initial_value: '0'  # 0..100

sensor:
  - platform: ads1115
    id: ads1115_ch0_raw
    multiplexer: 'A0_GND'
    gain: 4.096
    filters:
    - multiply: 3.09324980380745
    update_interval: 10s
    name: "ADS1115 A0-GND"
  - platform: template
    name: "Pumpe Sollwert Sensor"
    id: pump_percent_sensor
    lambda: 'return id(pump_percent);'
    update_interval: 10s
    unit_of_measurement: "%"
    accuracy_decimals: 0
    icon: "mdi:pulse"
    on_value:
      then:
        - lambda: |-
            id(pump_voltage).set_level(x/100);
  - platform: uptime
    name: Uptime Sensor

output:
  - platform: gpio
    pin: GPIO16
    id: gpio_16
  - platform: gp8403
    id: pump_voltage
    gp8403_id: DFR0971
    channel: 0

button:
  - platform: template
    name: "Pumpenleistung +5%"
    on_press:
      - lambda: |-
          id(pump_percent) += 5;
          if (id(pump_percent) > 100) id(pump_percent) = 100;
          id(pump_voltage).set_level(id(pump_percent)/100);
          id(pump_power_number).publish_state(id(pump_percent));
  - platform: template
    name: "Pumpenleistung -5%"
    on_press:
      - lambda: |-
          id(pump_percent) -= 5;
          if (id(pump_percent) < 0) id(pump_percent) = 0;
          id(pump_voltage).set_level(id(pump_percent)/100);
          id(pump_power_number).publish_state(id(pump_percent));
  - platform: template
    name: "Pumpe Aus"
    on_press:
      - lambda: |-
          id(pump_percent) = 0;
          id(pump_voltage).set_level(0);
          id(pump_power_number).publish_state(0);

# Onboard RGB-LED
light:
  - platform: status_led
    name: "State"
    pin: GPIO2
  - platform: neopixelbus
    type: GRB
    variant: WS2811
    pin: GPIO5
    num_leds: 1
    name: "NeoPixel Light"

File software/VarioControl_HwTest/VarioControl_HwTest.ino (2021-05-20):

/*
  VarioControl - Hardware Test

  No description.

  created 2021/05/20
  by Ruemmler, Elias
  modified 2021/05/20
  by Ruemmler, Elias

  Find the full project on GitHub:
  https://github.com/100prznt/VarioControl
*/


#include <Adafruit_DS3502.h>


#define LED_STATUS D3 //LOW to on (GPIO0)
#define LED_ERROR D4  //HIGH to on (GPIO2)
#define EN_PUMP D0    //HIGH to enable pump, LED on (GPIO16)

#define OW_DATA D7    //GPIO13

#define SW_MODE1 D5   //GPIO14
#define SW_MODE2 D8   //GPIO15

#define PRESSURE_AI A0 //Analog input for pressure sensor


Adafruit_DS3502 ds3502 = Adafruit_DS3502();


void setup() {
  Serial.begin(9600);
  // Wait until serial port is opened
  while (!Serial)
  {
    delay(1);
  }

  Serial.println();
  Serial.println("VarioControl - Hardware Test");


  Serial.println();
  Serial.println("Initialize GPIOs");
  Serial.println("- Outputs");
  pinMode(LED_STATUS, OUTPUT);
  pinMode(LED_ERROR, OUTPUT);
  pinMode(EN_PUMP, OUTPUT);
  Serial.println("  turn LEDs off");
  digitalWrite(LED_STATUS, HIGH);
  digitalWrite(LED_ERROR, LOW);
  digitalWrite(EN_PUMP, LOW);
  Serial.println("  successful");


  Serial.println("- Inputs");
  pinMode(SW_MODE1, INPUT);
  pinMode(SW_MODE2, INPUT);
  Serial.println("  successful");

  Serial.println("Initialize DS3502");
  if (!ds3502.begin())
  {
    Serial.println("  Couldn't find DS3502 chip");
    while (1);
  }
  Serial.println("  Found DS3502 chip");
}

void readAnalogInput()
{
  Serial.println("Start reading analog input...");
  
  int sensorValue = analogRead(PRESSURE_AI);
  // Convert the analog reading (which goes from 0 - 1023) to a voltage (0 - 10V):
  float voltage = sensorValue * (10.0 / 1023.0);
  // print out the value you read:
  Serial.print("Analog value: ");
  Serial.println(voltage);
}


void loop()
{  
  digitalWrite(LED_ERROR, LOW);
  delay(800);
  digitalWrite(LED_ERROR, HIGH);
  delay(400);
  readAnalogInput();
}

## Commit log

2021-04-23 Add layout
    [vc_board_v011.brd, vc_board_v011.sch]
2021-04-26 Update PCB
    [vc_board_v011.brd, vc_board_v011.sch]
2021-04-26 update layout
    [vc_board_v011.brd]
2021-04-27 PCB ORDER!
    [vc_board_v011.brd, vc_board_v011.sch]
2021-04-28 Update values
    [vc_board_v011.brd, vc_board_v011.sch]
2021-05-20 Update docu
    [vc_board_v011.xlsx]

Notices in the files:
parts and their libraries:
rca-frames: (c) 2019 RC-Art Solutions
